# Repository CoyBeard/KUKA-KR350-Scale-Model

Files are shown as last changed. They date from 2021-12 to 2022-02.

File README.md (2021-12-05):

# KUKA-KR350-Scale-Model
One fourth scale model of the KUKA KR350 model 3D printed and Arduino controlled.

NOTE: All Files Are V1 Unless In V2 Folder

All parts were printed in PLA 50% infil
The bolts and thread inserts are all in metric
All parts were purchased on Amazon

NOTE: some CAD files may be missing. They were moved around when I got a new hard drive.

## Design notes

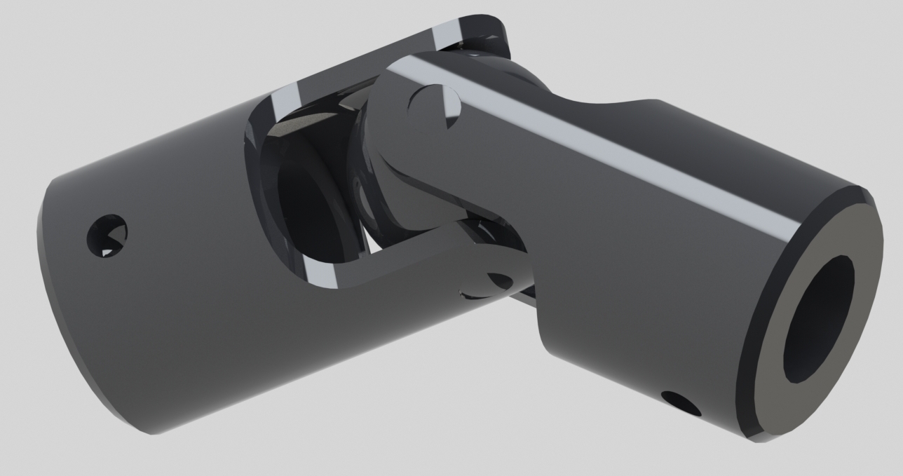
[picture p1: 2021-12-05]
u-joint-11.snapshot.5/ASSY_BERG_UJ3_RENDER (2021_06_28 15_48_35 UTC).JPG

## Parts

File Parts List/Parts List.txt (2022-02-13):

KR350 ¼ Scale Model Parts List:

uxcell Timing Belt 308mm Circumference 6mm Width Closed Fit Synchronous Pulley Wheel for 3D Printer:
https://www.amazon.com/gp/product/B07X88WRLK/ref=ppx_yo_dt_b_search_asin_title?ie=UTF8&psc=1

BEMONOC Pack of 10pcs 320-2GT-6 Industrial Timing Belt in Closed Loop 2GT Rubber Belt L=320mm W=6mm 160 Teeth for 3D Printer Parts:

https://www.amazon.com/gp/product/B014SMT8DA/ref=ppx_yo_dt_b_search_asin_title?ie=UTF8&psc=1

GT2 Idler Pulley Timing Belt Pulley 16 Teeth 3mm Bore for 3D Printer CNC 6mm Width Belt Pack of 10:

https://www.amazon.com/gp/product/B07K8CRT8N/ref=ppx_yo_dt_b_search_asin_title?ie=UTF8&th=1

Apex RC Products 10 Pack 5x8x2.5mm Rubber Shielded Ball Bearings MR85-2RS 1911R:

https://www.amazon.com/gp/product/B019I3PGWG/ref=ppx_yo_dt_b_search_asin_title?ie=UTF8&psc=1

uxcell 6001-2RS Ball Bearing 12mm x 28mm x 8mm Double Sealed 180101 Deep Groove Bearings High Carbon Steel Z1 (Pack of 8):

https://www.amazon.com/gp/product/B07FDXPVLP/ref=ppx_yo_dt_b_search_asin_title?ie=UTF8&psc=1

uxcell 6808-2RS Deep Groove Ball Bearings 40mm Inner Dia 52mm OD 7mm Bore Double Sealed Chrome Steel Z2 4pcs:

https://www.amazon.com/gp/product/B082PYSPR6/ref=ppx_yo_dt_b_search_asin_title?ie=UTF8&th=1

uxcell 6805-2RS Deep Groove Ball Bearings 25mm Inner Dia 37mm OD 7mm Bore Double Sealed Chrome Steel Z2 10pcs:

https://www.amazon.com/gp/product/B082PYT33D/ref=ppx_yo_dt_b_search_asin_title?ie=UTF8&th=1

ERYONE PLA Filament 1.75mm, 3D Printer Filament PLA , +/-0.03mm, 1kg(2.2lbs)/Spool, Orange:

https://www.amazon.com/gp/product/B07GNGGDNG/ref=ppx_yo_dt_b_search_asin_title?ie=UTF8&th=1

OVERTURE PLA Filament 1.75mm PLA 3D Printer Consumables, 1kg Cardboard Spool (2.2lbs), Dimensional Accuracy +/- 0.03mm, Fit Most FDM Printer (Space Gray):

https://www.amazon.com/gp/product/B07PDW8QWJ/ref=ppx_yo_dt_b_search_asin_title?ie=UTF8&psc=1

OVERTURE PLA Filament 1.75mm PLA 3D Printer Consumables, 1kg Cardboard Spool (2.2lbs), Dimensional Accuracy +/- 0.03mm, Fit Most FDM Printer (Black 1-Pack):

https://www.amazon.com/gp/product/B07PGY2JP1/ref=ppx_yo_dt_b_search_asin_title?ie=UTF8&th=1

4 Packs 5mm to 5mm Steel Universal Joint Cardan Coupling Connector, Rotatable Model DIY Motor Shaft Fitting Accessory for RC Car Boat with 8 Screws an:

UNAVAILABLE

uxcell 5mm x 300mm 304 Stainless Steel Solid Round Rod for DIY Craft - 10pcs:

https://www.amazon.com/gp/product/B082ZNZNXW/ref=ppx_yo_dt_b_search_asin_title?ie=UTF8&psc=1

uxcell M5 x 150mm 304 Stainless Steel Fully Threaded Rod Bar Studs Hardware 10 Pcs:

https://www.amazon.com/gp/product/B01M5DGV0P/ref=ppx_yo_dt_b_search_asin_title?ie=UTF8&psc=1

Glarks 370Pcs M2 M3 M4 M5 Female Thread Knurled Brass Threaded Insert Embedment Nut Assortment Kit for 3D Printing:

https://www.amazon.com/gp/product/B07L96KVP3/ref=ppx_yo_dt_b_search_asin_title?ie=UTF8&psc=1

1235PCS Hex Socket Screws Assortment Kit, M2 M3 M4 M5 Screw Bolts Nuts Washers Assortment Set with Allen Wrench, 14.9 Grade Carbon Alloy Steel, White Box:

https://www.amazon.com/gp/product/B091FGQSTJ/ref=ppx_yo_dt_b_search_asin_title?ie=UTF8&psc=1

3D Printer CNC Controller Kit with for ArduinoIDE, Longruner GRBL CNC Shield Board+RAMPS 1.4 Mechanical Switch Endstop DRV8825 A4988 Stepper Motor Driver Nema 17 Stepper Motor LKB02:

https://www.amazon.com/gp/product/B072N4FMRN/ref=ppx_yo_dt_b_search_asin_title?ie=UTF8&psc=1

Liberty 22mm mounting Hole Latch Emergency Stop Button Switch red, with 60mm Emergency Stop Sign 1NO 1NC, 660V 10A (4PCS):

https://www.amazon.com/gp/product/B08ZCDHZ3R/ref=ppx_yo_dt_b_search_asin_title?ie=UTF8&psc=1

Zixtec 10 Pack LM2596 DC-DC Buck Converter Step Down Module Power Supply DIP Output 1.25V-30V 3A (ZT001):

https://www.amazon.com/gp/product/B07VVXF7YX/ref=ppx_yo_dt_b_search_asin_title?ie=UTF8&psc=1

Toggle Switch Submini SPDT & DPDT On Off On Latching, Momentary, Short Shaft, Switch Assortment Kit, 31 pcs, 10 Types:

https://www.amazon.com/gp/product/B08T5XS9Q3/ref=ppx_yo_dt_b_search_asin_title?ie=UTF8&psc=1

eTopxizu 12v 30a Dc Universal Regulated Switching Power Supply 360w for CCTV, Radio, Computer Project:

https://www.amazon.com/gp/product/B00D7CWSCG/ref=ppx_yo_dt_b_search_asin_title?ie=UTF8&psc=1

ELEGOO UNO Project Super Starter Kit with Tutorial and UNO R3 Compatible with Arduino IDE:

https://www.amazon.com/gp/product/B01D8KOZF4/ref=ppx_yo_dt_b_search_asin_title?ie=UTF8&psc=1

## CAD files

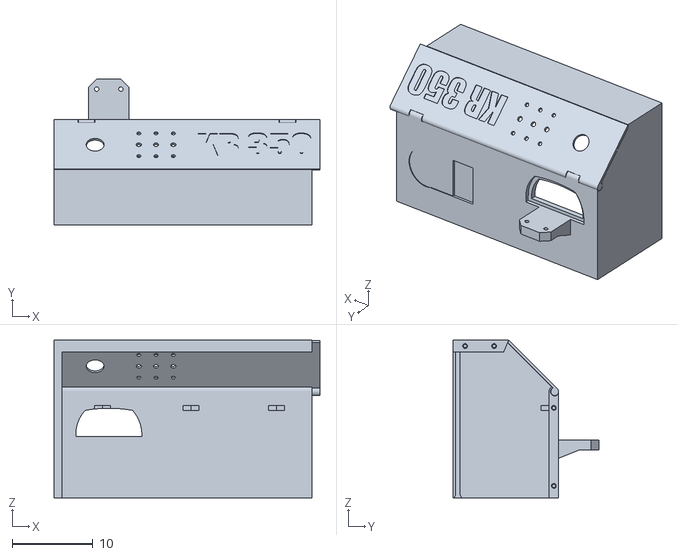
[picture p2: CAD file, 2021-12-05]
V2/Electronics Housing Main V2.stl
33.0 x 18.1 x 19.6

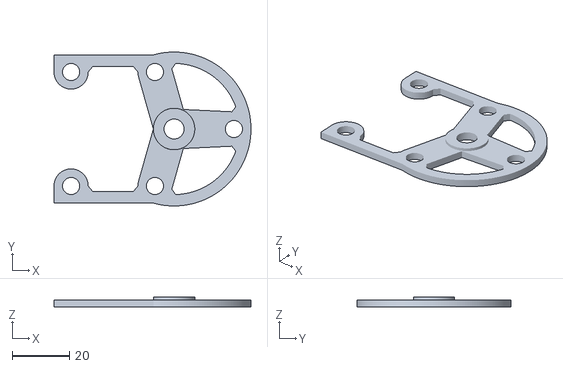
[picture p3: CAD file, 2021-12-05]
V2/STLs/V5/Wrist Main Plate Cover Bearing Insert.stl
69.1 x 54.0 x 3.50

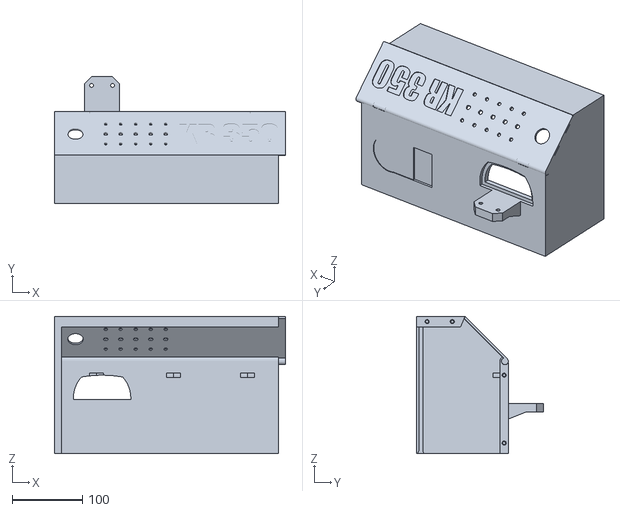
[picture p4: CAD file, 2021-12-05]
V2/STLs/V5/Electronics Housing Main (2021_08_29 19_09_18 UTC).stl
330.0 x 181.0 x 196.0

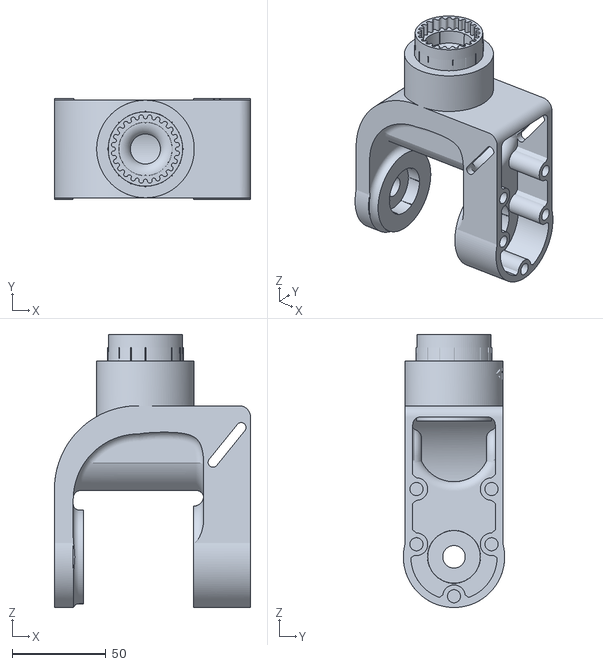
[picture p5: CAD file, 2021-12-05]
STLs/V6/4th Axis Barrel (2021_07_18 00_04_28 UTC).stl
104.5 x 54.0 x 145.5

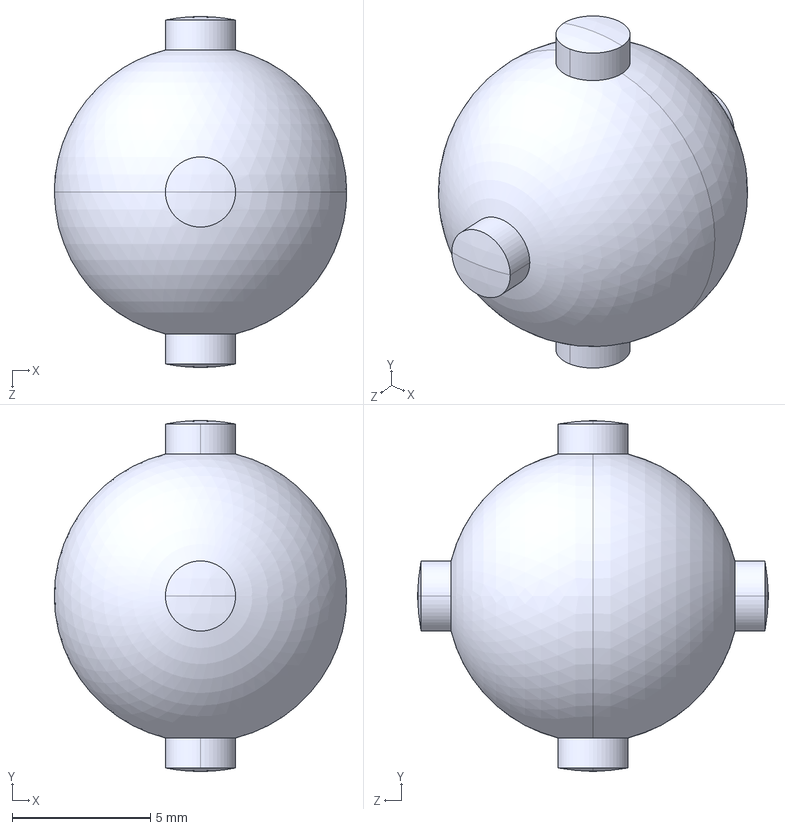
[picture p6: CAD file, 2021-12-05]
u-joint-11.snapshot.5/UJ-3_BALL (2021_06_28 15_48_35 UTC).STEP
10.6 x 12.7 x 12.7 mm

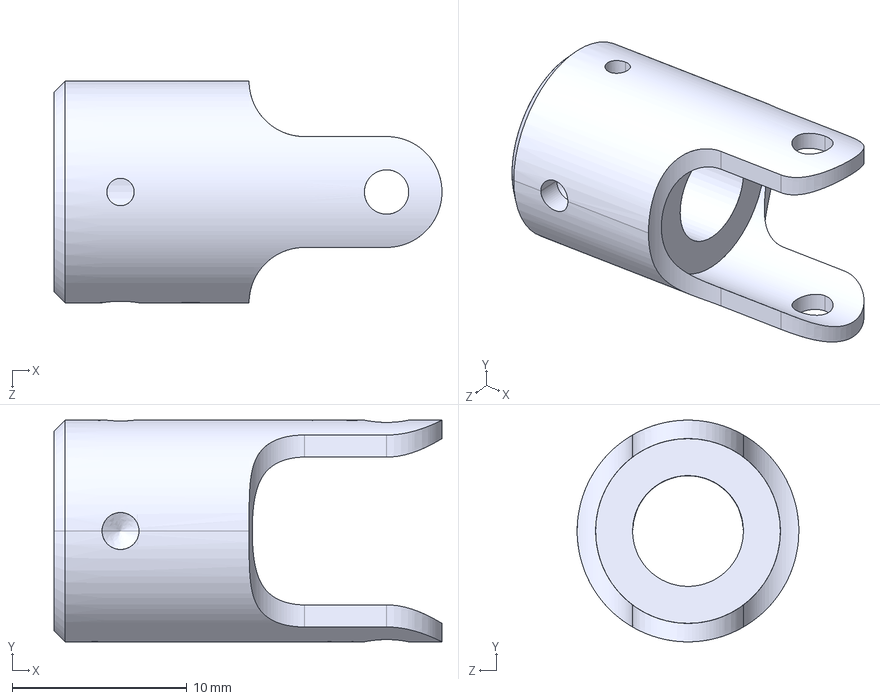
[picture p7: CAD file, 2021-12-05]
u-joint-11.snapshot.5/UJ-3_YOKE (2021_06_28 15_48_35 UTC).IGS
22.2 x 12.7 x 12.7 mm

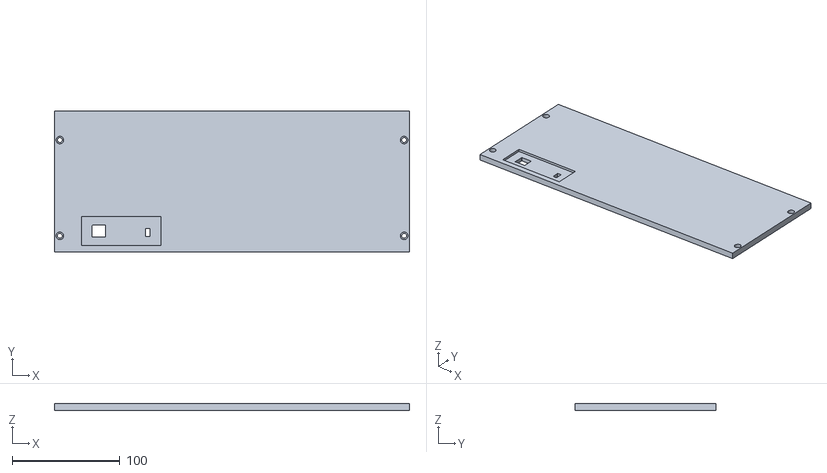
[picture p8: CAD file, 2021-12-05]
V2/STLs/V5/Electronics Housing Back Pannel (2021_08_29 19_09_18 UTC).stl
330.0 x 131.0 x 6.50

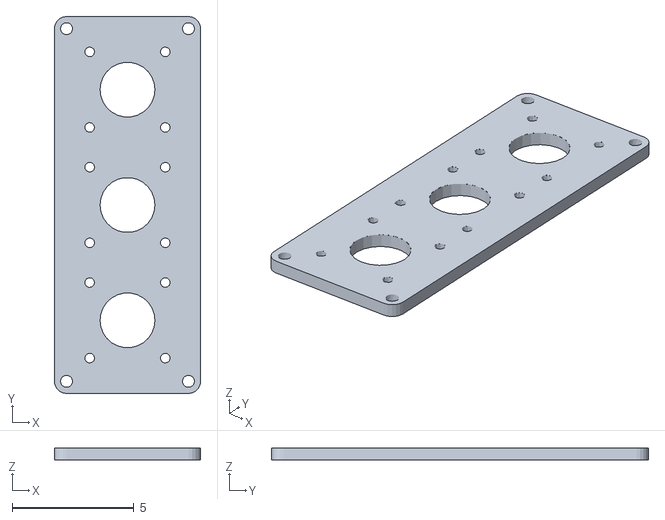
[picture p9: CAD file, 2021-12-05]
V2/STLs/V5/Forarm Motor Mounting Plate.stl
6.00 x 15.5 x 0.5

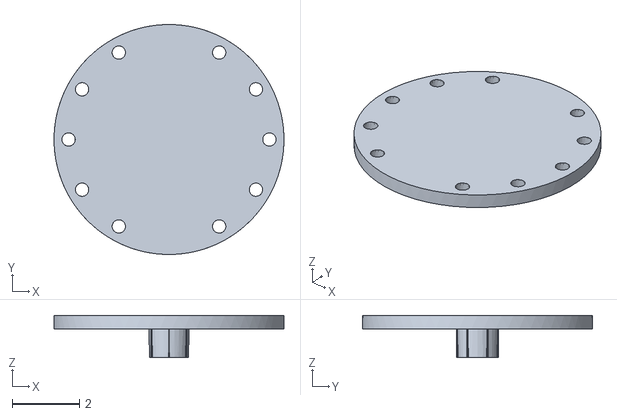
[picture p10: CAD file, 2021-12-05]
V2/STLs/V5/Wrist Axis 5 Mounting Plate.stl
6.82 x 6.81 x 1.25

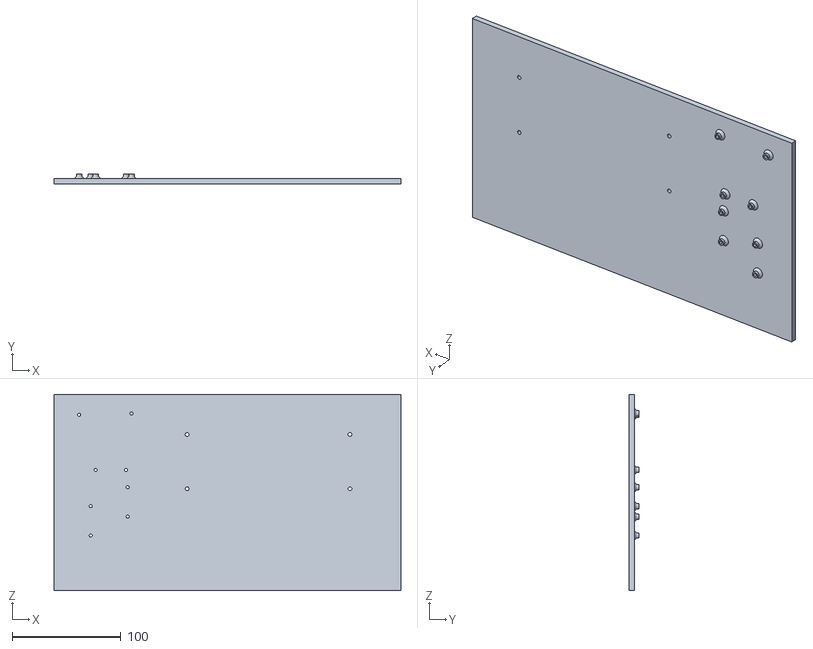
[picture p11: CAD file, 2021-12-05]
V2/STLs/V5/Electronics Housing Bottom Pannel (2021_08_29 19_09_18 UTC).stl
319.6 x 9.00 x 180.9

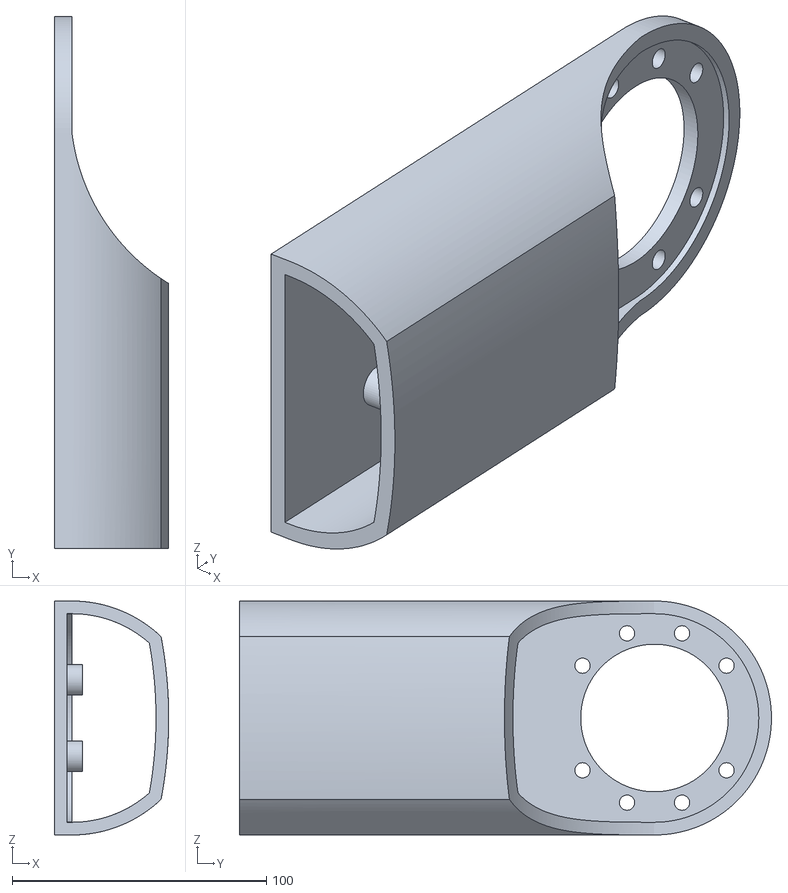
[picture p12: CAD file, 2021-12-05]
V2/STLs/V5/Bicep Frame (2021_08_29 19_09_18 UTC).stl
45.0 x 209.2 x 92.0

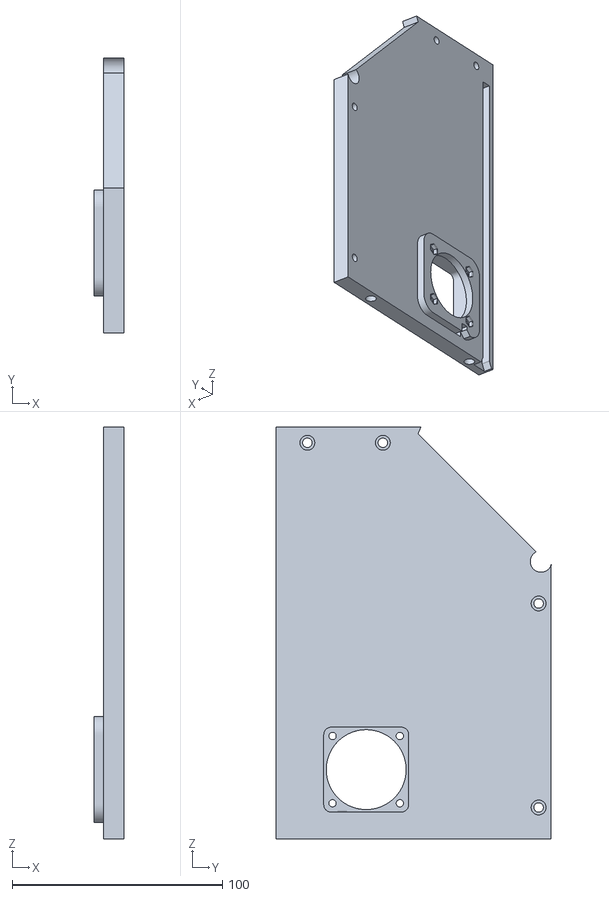
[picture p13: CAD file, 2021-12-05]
V2/STLs/V5/Electronics Housing Right Pannel (2021_08_29 19_09_18 UTC).stl
14.4 x 131.0 x 196.0

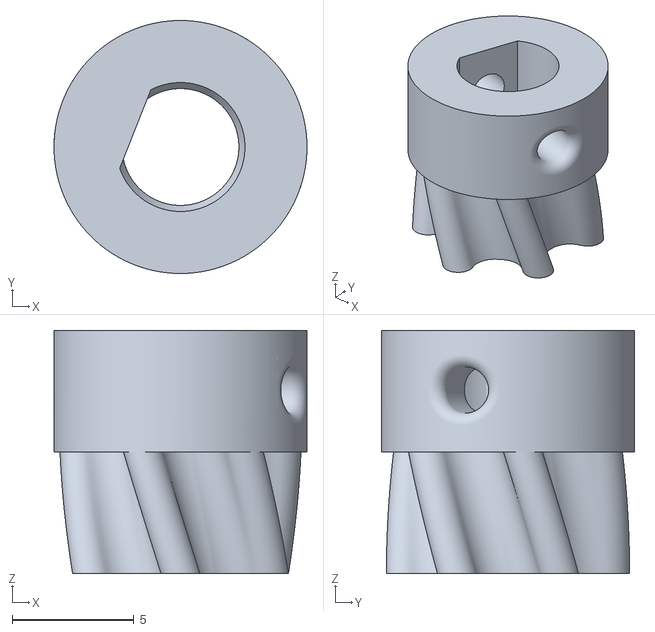
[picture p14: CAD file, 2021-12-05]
V2/STLs/V5/M5 6 Tooth D Profile Helical Drive Gear.stl
10.4 x 10.4 x 10.0

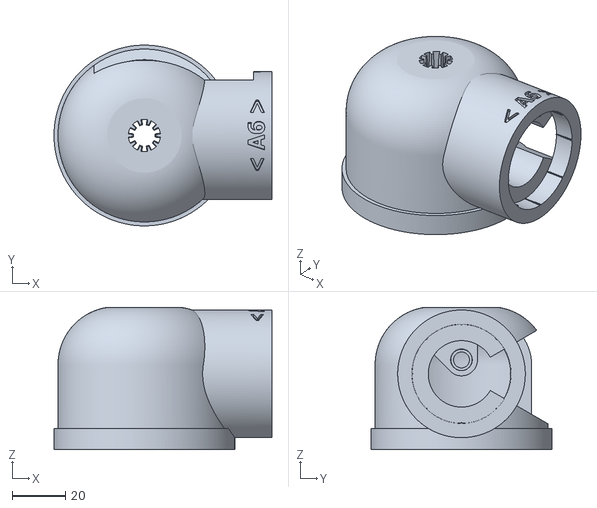
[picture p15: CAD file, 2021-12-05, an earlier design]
STLs/V2/Axis 6 Gearbox Main (2021_07_01 04_03_57 UTC).stl
82.0 x 68.0 x 53.5

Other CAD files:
V2/STLs/V4/Wrist Main Plate Cover Main (2021_08_28 20_24_39 UTC).stl
V2/STLs/V3/Wrist Main Plate Cover (2021_08_15 23_37_01 UTC).stl
STLs/V1/4th Axis Main Drive Gear (2021_06_30 15_27_50 UTC).stl
12x28x8mm Bearing (2021_06_27 04_15_50 UTC).ipt
20mm Bearing (2021_06_26 18_36_30 UTC).ipt
25x37x7mm Bearing (2021_06_29 15_13_14 UTC).ipt
3rd Axis (2021_07_17 17_44_58 UTC).ipt
3rd Axis Motor Mounts (2021_07_05 19_41_37 UTC).ipt
40mm Bearing (2021_06_28 21_53_51 UTC).ipt
4th 5th and 6th Axes Model Assembly (2021_08_06 20_10_39 UTC).iam
4th Axis Barrel (2021_07_18 00_04_28 UTC).ipt
4th Axis Drive Gear Slotteds (2021_07_14 22_00_42 UTC).ipt
4th Axis Drive Gears (2021_07_17 17_44_58 UTC).ipt
4th Axis Main Drive Gear (2021_07_17 17_44_58 UTC).ipt
5mm Bearing (2021_06_26 18_36_30 UTC).ipt
5mm Coupler (2021_07_17 17_44_58 UTC).ipt
5th Axis Cover (2021_06_30 20_31_55 UTC).ipt
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

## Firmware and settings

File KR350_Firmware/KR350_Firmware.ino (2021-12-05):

#include <AccelStepper.h>
#include <MultiStepper.h>

const int stepA4 = 2;
const int dirA4  = 5;

const int stepA5 = 3;
const int dirA5  = 6;

const int stepA6 = 4;
const int dirA6  = 7;


const int Pos4 = A3;
const int Neg4  = 11;

const int Pos5 = 10;
const int Neg5  = 13;

const int Pos6 = 9;
const int Neg6  = 12;

//Bolian
int StartupSequenceRan = false;

// Define some steppers and the pins the will use
AccelStepper Axis4(AccelStepper::DRIVER, stepA4, dirA4);
AccelStepper Axis5(AccelStepper::DRIVER, stepA5, dirA5);
AccelStepper Axis6(AccelStepper::DRIVER, stepA6, dirA6);

void setup() 
{  
    Serial.begin(9600);

    pinMode(8, OUTPUT); // **** set the enable pin to output
    digitalWrite(8, LOW); // *** set the enable pin low
  
    pinMode(stepA4,OUTPUT);
    pinMode(dirA4,OUTPUT);
  
    pinMode(stepA5,OUTPUT);
    pinMode(dirA5,OUTPUT);
  
    pinMode(stepA6,OUTPUT);
    pinMode(dirA6,OUTPUT);

    pinMode(Pos4, INPUT);
    pinMode(Neg4, INPUT);
    
    pinMode(Pos5, INPUT);
    pinMode(Neg5, INPUT);
    
    pinMode(Pos6, INPUT);
    pinMode(Neg6, INPUT);
    
  
    Axis4.setMaxSpeed(100000000.0);//800
    Axis4.setAcceleration(3000.0);
    
    Axis5.setMaxSpeed(100000000.0);//10000
    Axis5.setAcceleration(30000.0);
    
    Axis6.setMaxSpeed(10000.0);//10000
    Axis6.setAcceleration(3000.0);



}

void StartupSequence() {
    Axis4.setMaxSpeed(10000.0);
    Axis5.setMaxSpeed(10000.0);
    Axis6.setMaxSpeed(10000.0);
    Axis4.moveTo(0);//2100
    Axis5.move(5000);//5000
    Axis6.moveTo(0); //5000
    while (Axis4.distanceToGo() !=  0 || Axis5.distanceToGo() != 0 || Axis6.distanceToGo() != 0) {
      Axis4.run();
      Axis5.run();
      Axis6.run();
    } if (Axis4.distanceToGo() == 0 && Axis5.distanceToGo() == 0 && Axis6.distanceToGo() == 0) {
      Serial.print("Move one complete");
      Serial.print("\n");
      delay(500);
    }

    Axis4.setMaxSpeed(10000.0);
    Axis5.setMaxSpeed(10000.0);
    Axis6.setMaxSpeed(10000.0);
    Axis4.moveTo(-3000);//2100
    Axis5.move(-3000);//5000
    Axis6.moveTo(0); //5000
    while (Axis4.distanceToGo() !=  0 || Axis5.distanceToGo() != 0 || Axis6.distanceToGo() != 0) {
      Axis4.run();
      Axis5.run();
      Axis6.run();
    } if (Axis4.distanceToGo() == 0 && Axis5.distanceToGo() == 0 && Axis6.distanceToGo() == 0) {
      Serial.print("Move two complete");
      Serial.print("\n");
      delay(500);
    }

    Axis4.setMaxSpeed(1100.0);
    Axis5.setMaxSpeed(100000.0);
    Axis6.setMaxSpeed(10000.0);
    Axis4.move(-3000);//2100
    Axis5.move(0);//5000
    Axis6.move(-7000); //5000
    while (Axis4.distanceToGo() !=  0 || Axis5.distanceToGo() != 0 || Axis6.distanceToGo() != 0) {
      Axis4.run();
      Axis5.run();
      Axis6.run();
    } if (Axis4.distanceToGo() == 0 && Axis5.distanceToGo() == 0 && Axis6.distanceToGo() == 0) {
      Serial.print("Move three complete");
      Serial.print("\n");
      delay(500);
    }

    Axis4.setMaxSpeed(10000.0);
    Axis5.setMaxSpeed(10000.0);
    Axis6.setMaxSpeed(10000.0);
    Axis4.move(0);//2100
    Axis5.move(5000);//5000
    Axis6.move(0); //5000
    while (Axis4.distanceToGo() !=  0 || Axis5.distanceToGo() != 0 || Axis6.distanceToGo() != 0) {
      Axis4.run();
      Axis5.run();
      Axis6.run();
    } if (Axis4.distanceToGo() == 0 && Axis5.distanceToGo() == 0 && Axis6.distanceToGo() == 0) {
      Serial.print("Move four complete");
      Serial.print("\n");
      delay(500);
    }

    //Backlash Compensation
    Axis4.setMaxSpeed(10000.0);
    Axis4.move(600);
    while (Axis4.distanceToGo() !=  0) {
      Axis4.run();
    }
    
    Axis4.setMaxSpeed(10000.0);
    Axis5.setMaxSpeed(10000.0);
    Axis6.setMaxSpeed(10000.0);
    Axis4.move(3000);//2100
    Axis5.move(3000);//5000
    Axis6.move(0); //5000
    while (Axis4.distanceToGo() !=  0 || Axis5.distanceToGo() != 0 || Axis6.distanceToGo() != 0) {
      Axis4.run();
      Axis5.run();
      Axis6.run();
    } if (Axis4.distanceToGo() == 0 && Axis5.distanceToGo() == 0 && Axis6.distanceToGo() == 0) {
      Serial.print("Move five complete");
      Serial.print("\n");
      delay(500);
    }
    
    Axis4.setMaxSpeed(550.0);
    Axis5.setMaxSpeed(10000.0);
    Axis6.setMaxSpeed(3000.0);
    Axis4.move(2100);//2100
    Axis5.move(0);//5000
    Axis6.moveTo(0); //5000
    while (Axis4.distanceToGo() !=  0 || Axis5.distanceToGo() != 0 || Axis6.distanceToGo() != 0) {
      Axis4.run();
      Axis5.run();
      Axis6.run();
    } if (Axis4.distanceToGo() == 0 && Axis5.distanceToGo() == 0 && Axis6.distanceToGo() == 0) {
      Serial.print("Zero Position");
      Serial.print("\n");
      delay(3000);
    }

}

void ReadInputs() {
  Serial.print("Pos4: ");
  Serial.print(digitalRead(Pos4));
  Serial.print("\n");
  Serial.print("Neg4: ");
  Serial.print(digitalRead(Neg4));
  Serial.print("\n");
  Serial.print("Pos5: ");
  Serial.print(digitalRead(Pos5));
  Serial.print("\n");
  Serial.print("Neg5: ");
  Serial.print(digitalRead(Neg5));
  Serial.print("\n");
  Serial.print("Pos6: ");
  Serial.print(digitalRead(Pos6));
  Serial.print("\n");
  Serial.print("Neg6: ");
  Serial.print(digitalRead(Neg6));
  Serial.print("\n");
  delay(1000);
}

void loop()
{
  //Run Startup Sequence Once
  if (StartupSequenceRan == false) {
    StartupSequence();

    //Bolian
    StartupSequenceRan = true;
  }

  //ReadInputs();

  //Main

  Axis4.setMaxSpeed(10000.0);
  Axis5.setMaxSpeed(10000.0);
  Axis6.setMaxSpeed(10000.0);
    
  //Axis 6 Pos
  while (digitalRead(Pos4) == 1) {
    Axis6.move(1000);
    Axis6.run();
  }
  while (digitalRead(Pos4) == 0 && Axis6.distanceToGo() !=  0) {
    Axis6.run();
  }

  //Axis 6 Neg
  while (digitalRead(Neg4) == 1) {
    Axis6.move(-1000);
    Axis6.run();
  }
  while (digitalRead(Neg4) == 0 && Axis6.distanceToGo() !=  0) {
    Axis6.run();
  }

  //Axis 5 Pos
  while (digitalRead(Pos5) == 1) {
    Axis5.move(1000);
    Axis5.run();
  }
  while (digitalRead(Pos5) == 0 && Axis5.distanceToGo() !=  0) {
    Axis5.run();
  }

  //Axis 5 Neg
  while (digitalRead(Neg5) == 1) {
    Axis5.move(-1000);
    Axis5.run();
  }
  while (digitalRead(Neg5) == 0 && Axis5.distanceToGo() !=  0) {
    Axis5.run();
  }

  //Axis 4 Pos
  while (digitalRead(Pos6) == 1) {
    Axis4.move(1000);
    Axis4.run();
  }
  while (digitalRead(Pos6) == 0 && Axis4.distanceToGo() !=  0) {
    Axis4.run();
  }

  //Axis 4 Neg
  while (digitalRead(Neg6) == 1) {
    Axis4.move(-1000);
    Axis4.run();
  }
  while (digitalRead(Neg6) == 0 && Axis4.distanceToGo() !=  0) {
    Axis4.run();
  }

}
